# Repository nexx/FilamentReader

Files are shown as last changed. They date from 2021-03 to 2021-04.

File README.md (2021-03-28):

# FilamentReader
This repository contains the source code, BOM, wiring details and 3D printed components for an encoder based filament reader using an Arduino Nano.

The following parts are currently required:
* 1x LPD3806-600BM-G5-24C Rotary Encoder
* 1x 608-2RS bearing
* 2x 2.5x10mm O-rings
* 3x M3x6 Socket head cap screws
* 3x M3x16 Socket head cap screws
* 3x M3 Nyloc nuts
* 1x Arduino Nano
* Arduino Nano or compatible clone

Print one of each component in the STL directory.

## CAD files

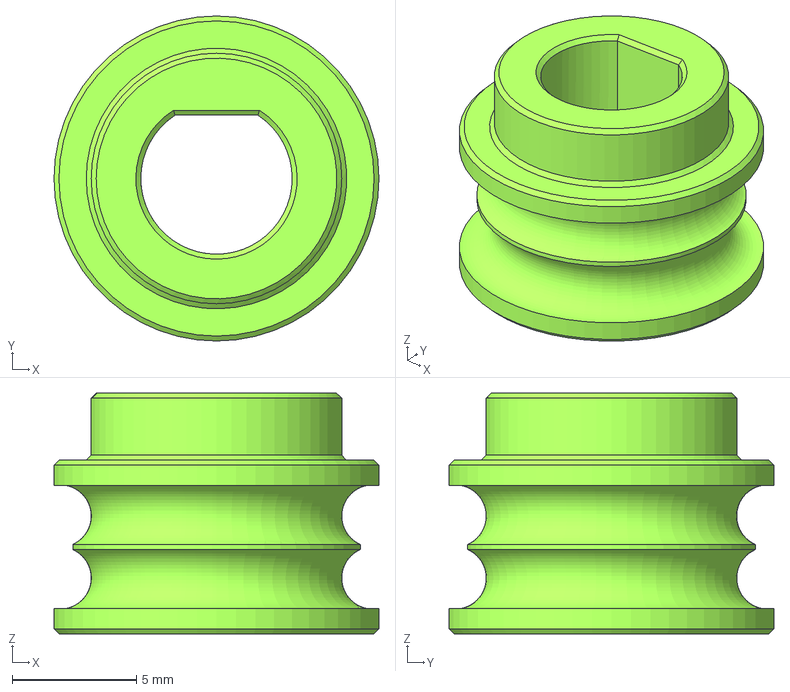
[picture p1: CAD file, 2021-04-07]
step/encoder_wheel.step
13.1 x 13.1 x 9.70 mm

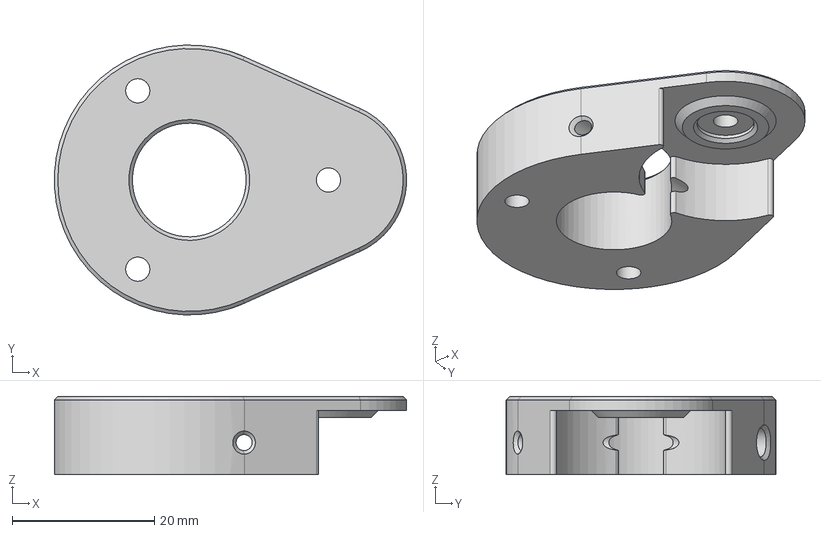
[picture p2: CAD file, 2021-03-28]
step/encoder_body_top.step
49.5 x 38.0 x 11.0 mm

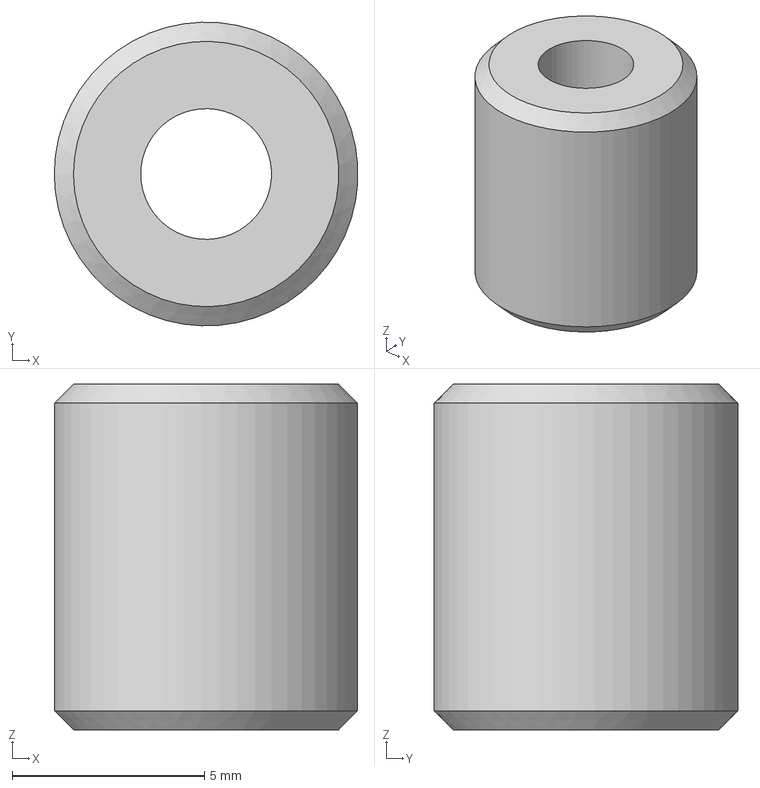
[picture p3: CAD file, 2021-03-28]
step/encoder_body_bearing_pin.step
7.89 x 7.90 x 9.00 mm

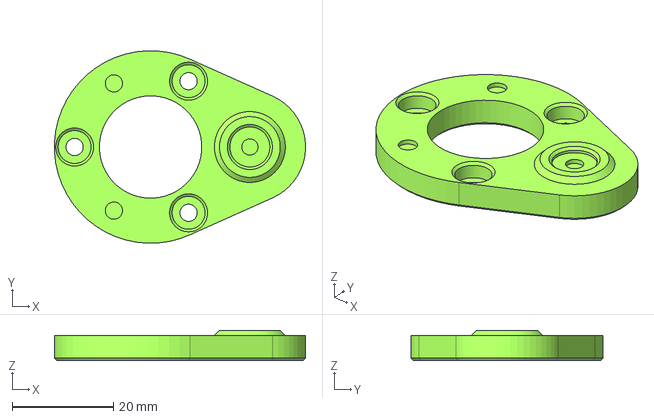
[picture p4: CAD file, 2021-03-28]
step/encoder_body_base.step
49.5 x 38.0 x 6.00 mm

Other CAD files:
stl/encoder_body_base.stl
stl/encoder_body_bearing_pin.stl
stl/encoder_body_top.stl
stl/encoder_wheel.stl

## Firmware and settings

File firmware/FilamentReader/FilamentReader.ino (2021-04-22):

/* Filament Reader
 * 
 * Copyright (c) 2021 Simon Davie <nexx@nexxdesign.co.uk>
 * 
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
 * You should have received a copy of the GNU General Public License
 * along with this program.  If not, see <https://www.gnu.org/licenses/>.
 */

#include <EEPROM.h>
#include <Encoder.h>
Encoder filamentEncoder(2, 3);

// Constant vars
const char compile_date[] = __DATE__ " " __TIME__;
const float compile_version = 1.1;

// Diameter of the gear or wheel attached to the encoder, this can be
// tweaked as necessary to achieve accurate results.
// MK8 Extruder gear    = ~11.00
float gearDiameter = 10.9885;

// Number of pulses produces by the encoder for one full rotation.
// This is normally mentioed in the spec sheet.
// LPD3806-600BM-G5-24C = 2400
// AMT102-V (2048 PPR)  = 8192
const unsigned int encoderRotationCount = 8192;

// Used to store the calculated encoder per MM value.
float encoderCountPerMM = 0.00;

// Polling intverval in ms
int interval = 500;

// State tracking
bool measureActive = false;
String serialData = "";
bool serialDataComplete = false;

// Used to track extruded amount
unsigned long currentMeasurement = 0;
unsigned long previousMeasurement = 0;

// Mode selection
bool report_relative = false;

void setup() {
  // Open the serial port at 9600 baud.
  Serial.begin(9600);
  serialData.reserve(32);

  // Check the EEPROM for the calibrated value, use that if
  // it exists and is valid.
  float calEEPROM = 0.00;
  EEPROM.get(0, calEEPROM);
  if (!isnan(calEEPROM) && calEEPROM != 0) {
    gearDiameter = calEEPROM;
  }

  // Output a welcome message
  Serial.print("NXE|");
  Serial.print(String(compile_version));
  Serial.print("|");
  Serial.print(String(compile_date));
  Serial.print("|");
  Serial.print(interval);
  Serial.print("|");
  Serial.println(gearDiameter, 6);

  // Calculate the encoder pulses required for 1mm of movement.
  encoderCountPerMM = encoderRotationCount / (gearDiameter * PI);
  
  // Reset the encoder
  resetEncoder();
}

void loop() {
  // Capture the encoder reading prior to anything else
  currentMeasurement = filamentEncoder.read();
  float result = 0;

  // Handle incoming serial data
  if (serialDataComplete) {
    if (serialData.startsWith("ABS")) {
      report_relative = false;
    } else if (serialData.startsWith("REL")) {
      report_relative = true;
    } else if (serialData.startsWith("START")) {
      resetEncoder();
      measureActive = true;
    } else if (serialData.startsWith("INTERVAL")) {
      serialData = serialData.substring(8);
      if (serialData.toInt()) {
        interval = serialData.toInt();
      }
    } else if (serialData.startsWith("MEASURE")) {
      // Only reply if we're not actively measuring
      if (!measureActive) {
        Serial.println(currentMeasurement / encoderCountPerMM, 4);
      }
    } else if (serialData.startsWith("RESET")) {
      resetEncoder();
    } else if (serialData.startsWith("STOP")) {
      measureActive = false;
    } else if (serialData.startsWith("CAL")) {
      serialData = serialData.substring(3);
      if (serialData.toFloat()) {
        float calDistance = serialData.toFloat();
        float calDiameter = ((calDistance / currentMeasurement) * encoderRotationCount) / PI;
        Serial.print("CALIBRATED DIAMETER: ");
        Serial.println(calDiameter, 6);

        // Save calibration to EEPROM
        EEPROM.put(0, calDiameter);
        float calEEPROM = 0.00f;
        EEPROM.get(0, calEEPROM);
        if (calEEPROM != calDiameter) {
          Serial.print("ERROR SAVING TO EEPROM. EXPECTED: ");
          Serial.print(calDiameter);
          Serial.print(" RETRIEVED: ");
          Serial.print(calEEPROM);
        } else {
          Serial.println("CALIBRATION SAVED TO EEPROM");
        }
        encoderCountPerMM = encoderRotationCount / (calDiameter * PI);
      }
    }

    // Clear serial data and flag
    serialData = "";
    serialDataComplete = false;
  }

  // Run measurement if enabled
  // FIXME: Catch and handle the encoder rollover 0 > 4294967295
  if (measureActive) {
    if (report_relative) {
      if (currentMeasurement > previousMeasurement) {
        // We've extruded filament
        result = (currentMeasurement - previousMeasurement) / encoderCountPerMM;
      } else if (currentMeasurement < previousMeasurement) {
        // We've retracted filament
        result = 0 - ((previousMeasurement - currentMeasurement) / encoderCountPerMM);
      }
    } else {
      result = (currentMeasurement / encoderCountPerMM);
    }
    
    // Output result to the serial console to 4 decimal accuracy
    Serial.println(result, 4);
    previousMeasurement = currentMeasurement;
    delay(interval);
  }
}

// Used to reset the encoder stats to 0
void resetEncoder() {
  // Reset the encoder to 0
  filamentEncoder.write(0);

  // Reset our tracking variables
  currentMeasurement = 0;
  previousMeasurement = 0;
}

// Handle incoming serial data
void serialEvent() {
  while (Serial.available()) {
    char inChar = (char)Serial.read();
    serialData += inChar;
    if (inChar == '\n') {
      serialDataComplete = true;
    }
  }
}

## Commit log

2021-03-24 Create FilamentReader.ino
    Initial commit of Arduino code
2021-03-28 Release 0.9 beta
    [encoder_body_base.step, encoder_body_base.stl, encoder_body_bearing_pin.step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]
2021-03-28 Update FilamentReader.ino
    - Calibrate for new encoder wheel
    - Increase output accuracy to 3 decimal places
2021-03-29 Update FilamentReader.ino
    Expand firmware capabilities to allow data logging to be started, stopped and reset via the serial console. This is achieved by sending B, S or R to the device.
    Further, sending I <value> will adjust the polling rate when data is being returned.
    Returned data is now in the format of:
    <distance_since_last>,<total_distance>
    [FilamentReader.ino]
2021-04-07 Update FilamentReader.ino
    Significant improvements across the entire program.
    - Calibration support and EEPROM storage of calibrated value
    - Absolute and Relative reporting modes
    - Single-shot measurement
    - Configurable reporting interval
    - Handshake message on connection showing firmware version and build date.
2021-04-07 Update encoder wheel design
    Slightly tweaked design to improve filament grip.
    [encoder_wheel.step, encoder_wheel.stl]
2021-04-14 Update FilamentReader.ino
    - Move handshake into a command
    - Set serial speed to 9600 baud
2021-04-17 Update FilamentReader.ino
    Fix relative reporting
    [FilamentReader.ino]
2021-04-17 Update FilamentReader.ino
    - Move the handshake output back into setup() as it is handled differently in the GUI now
2021-04-22 Update FilamentReader.ino
    - Update defaults for AMT102-V encoder
    - Update defaults for MK8 drive gear
    - Fix statically defined 2400 PPR in calibration routine
    [FilamentReader.ino]

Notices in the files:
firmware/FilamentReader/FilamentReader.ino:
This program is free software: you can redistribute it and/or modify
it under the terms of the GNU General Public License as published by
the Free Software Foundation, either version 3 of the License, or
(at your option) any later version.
